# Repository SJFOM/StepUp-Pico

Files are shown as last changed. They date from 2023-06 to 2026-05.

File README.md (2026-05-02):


# *StepUp!* - A no-code tool for instant stepper motor testing

Badge






StepUp device with motor and PCBs

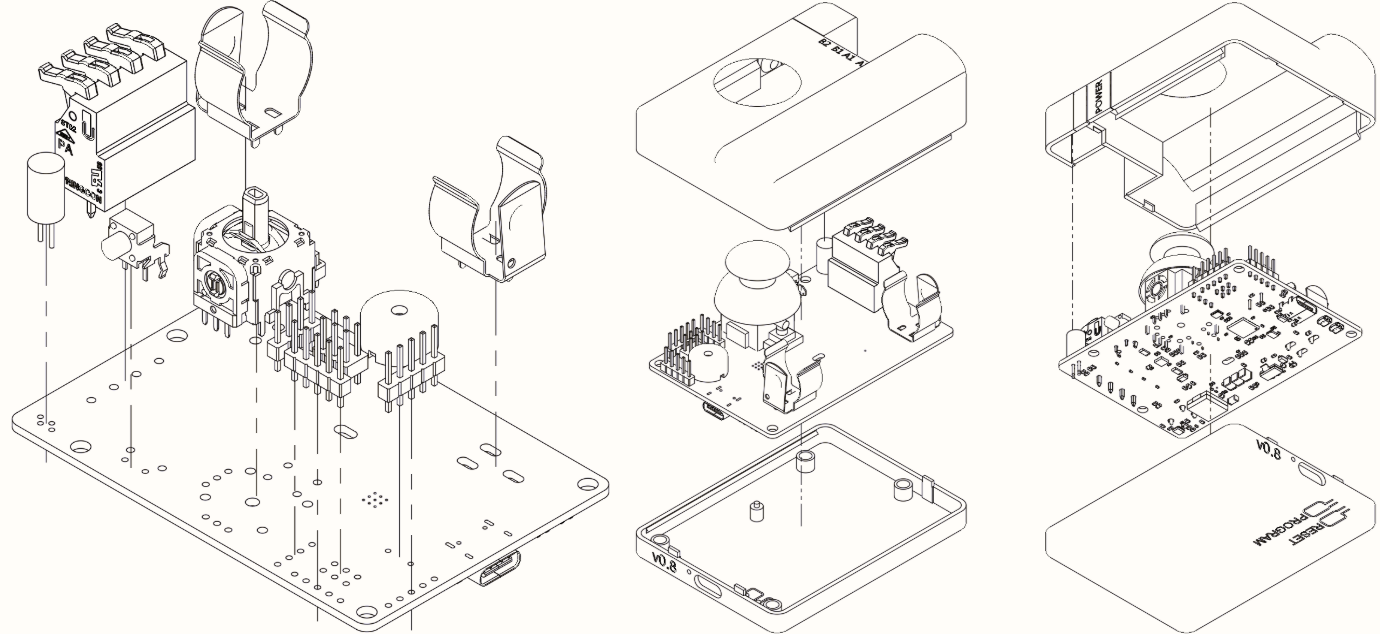
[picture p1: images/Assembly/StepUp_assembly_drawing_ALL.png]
StepUp device with motor


## What is it?
StepUp! is a low-cost, battery powered handheld device for quick testing and development work with any sized stepper motor - all you need is:

- A stepper motor
- A motor cable

## Why did you make it?

Working a lot with stepper motors, I often find myself wanting to test a single motor at a time to understand if its performing as it should - often with questions like:

- Is there an issue with my driving circuit or the motor itself?
- Is the cabling damaged or do the coils contain open or short circuits?
- Does it have a hold current or is it jammed?

I found that, to really answer these questions required power supplies, microcontrollers, stepper motor driving circuitry, a PC to compile and upload firmware and a programmatic approach to moving a motor. What I needed was a simpler way to control motors that felt intuitive - something battery powered and ideally joystick controlled.

I came to the realisation that this problem was two-fold:

1. I don’t have an easy & repeatable way of driving stepper motors
2. I don’t always have all of my lab equipment set up to make the kind of measurements I care about.

>I set out to tackle problem number 1 - creating an easy way to repeatably test a stepper motor

## What makes it special?

There are *plenty* of boards and solutions out there that can drive a stepper motor. However, what I have *yet to see* is a solution that is completely self-contained, requiring no external power supply and driving a stepper motor using input controls from an operator.

My aim is for this to be an item in your toolbox, one that can be called upon whenever you need to test a motor - without all the setup cost.

It is inherently low power - giving just enough juice to get a motor going but with enough power to test out some motor features.

## How much does it cost to build?
### Short answer
Around **€50 (or $60)** per unit

### *Longer answer...*
A core goal from the outset was to make this _as_ cheap as I possibly could. Totting up my most recent order for 5 PCB's with 3 assembled PCBA's and including the additional through-hole components I hand solder to the PCBA's (to reduce cost) works out to around $50 per PCB as per my last order in March 2025.

## Tech specs
- **Firmware:** Pico-SDK `v2.2.0` running FreeRTOS `v11.2.0`
- **CPU:** Dual-core Arm Cortex-M0+ processor, flexible clock running up to 133 MHz
- **RAM:** 264kB on-chip SRAM
- **Flash:** 2MB on-board QSPI flash
- **Battery:** 18650 Li-Ion, single cell (protected or non)
- **Charge current:** 300mA
- **Motor control:** ~10.2V at 500mA (default) -> 5.1 Watts
- **Battery life:** ~5.5 hours in testing using a `3400mAh` 18650 Li-Ion battery

# Pre-requisites

## Assembling a StepUp! device
All documentation and pre-requisites for creating your own StepUp! PCB and enclosure can be found in the [Hardware README file](./Hardware/README.md).

## IDEs

This project was developed using [Microsoft Visual Studio Code](https://code.visualstudio.com/) and all instructions which follow mention use of its code extensions for working with the StepUp! project. Workspace files are included herein - see [rp2040.code-workspace](./rp2040.code-workspace).

## Quick-start - cloning the repo and uploading code

1. Clone (recursively) the repo: `git clone --recursive https://github.com/SJFOM/StepUp-Pico.git`.
2. Enter the repo: `StepUp-Pico`.
3. Optionally, edit `CMakeLists.txt` and `/App-StepUp/CMakeLists.txt` to configure the project.
4. Optionally, manually configure the build process: `cmake -S . -B build/`.
5. Optionally, manually build the app: `cmake --build build`.
6. Connect your device so it’s ready for file transfer.
7. Copy the `StepUp.uf2` file from the `build/App-StepUp` folder to the drive which represents the attached Pico device hardware.

## VS Code extensions

### Required
Raspberry Pi's own [VSCode extension](https://github.com/raspberrypi/pico-vscode) simplifies the installation process for any OS. It includes other necessary VS Code extensions such as [CMake](https://marketplace.visualstudio.com/items?itemName=ms-vscode.cmake-tools) and [Cortex-Debug](https://github.com/marus/cortex-debug) for both CMake file compilation and debugging using OpenOCD via a SWD capable debugger probe respectively.

### Optional
While the Raspberry Pi Pico extension is the only one _required_ to compile code for this project, an ancilliary list of recommended extensions can be found in the included [`extensions.json`](./.vscode/extensions.json) file and will be prompted for install by the VS Code IDE.

## Project Structure

```
/StepUp-Pico
|
|___/App-StepUp             // StepUp! Application source code (C++)
|   |___CMakeLists.txt      // Application-level CMake config file
|
|___/Config
|   |___FreeRTOSConfig.h    // FreeRTOS project config file
|
|___/FreeRTOS-Kernel        // FreeRTOS kernel files, included as a submodule
|
|___/images                 // Image files used in the README.md guides
|
|___/Hardware               // Thin layers for global control - used as parent class
|   |___3D print files      // STL files to be 3D printed for StepUp housing
|   |___PCBA files          // Zip file containing Gerbers, Drill files & BoM 
|
|___/Interfaces             // Thin layers for global control - used as parent class
|
|___/Libraries              // Non-HW specific code, commonly used function calls
|
|___CMakeLists.txt          // Top-level project CMake config file
|___pico_sdk_import.cmake   // Raspberry Pi Pico SDK CMake import script
|
|___rp2040.code-workspace   // Visual Studio Code workspace
|
|___README.md
|___LICENSE.md
```

# Using the device

Steps `1` -> `3` below should be followed in the order provided to give best chances of uploading code first time!

If helpful, all PCB schematics for this project can be found in the [Releases section of my KiCad repository](https://github.com/SJFOM/KiCad/releases).

## 1. Inserting a battery
Only 18650 Li-Ion cells are supported by this device. The 18650 cell can either include battery protection circuitry or not - there is a battery protection circuit on-board the StepUp! device which is configured specifically for the device and will prevent device power-on if reverse polarity is detected. See the [Hardware README file](./Hardware/README.md) for reference on assembly process.

>**NOTE:** When first inserting the battery, you must also plug in a USB C cable to power up the device. This is a known quirk of the battery protection circuit which prohibits using the battery until external power is first applied.

## 2. Uploading code to the device

Once a battery has been inserted, plug the device into your PC using a USB C data cable. 

Due to a small hardware quirk, you need to ensure that the `POWER` button (on the side) is held down for the duration of the programming process. Follow these steps to upload code:
1. Press and hold the `POWER` button on the side of the PCB (or Enclosure box) and the `PROGRAM` button on the bottom of the PCB (or Enclosure box)
3. Press once the `RESET` button to reboot the device into program mode.
4. You can now release the `PROGRAM` button but keep the `POWER` button held down

The device should evaluate as a USB drive mounted to your PC. From here, you can copy the `StepUp.uf2` file to the mounted device either:
- By grabbing the latest copy of [Release firmware](https://github.com/SJFOM/StepUp-Pico/releases) available in the GitHub repo
- _OR_ - locating it in the `build/App-StepUp` directory once you have compiled this repository

Only _now_, once the device has been successfully programmed can you release the `POWER` button.

## 3. Powering ON
Once firmware has been loaded successfully - press and hold the `POWER` button on the side of the device until the LED flashes GREEN several times and an audible tone of increasing frequencies plays (like a step-up sequence).

## 4. Controlling the Motor
### Connection
Connect the stepper motor using the connector labelled with `A1, A2, B1, B2` to match the coils of the given motor, lifting the 4 black tabs of the connector to allow insertion of the wires and then closing each of the 4 black tabs down with an audible "click" once the wires are in place. The wires should ideally have at least 5mm of exposed wire to ensure a good connection.

### Joystick control
The Joystick is used to control the motor direction and speed. If you increase or decrease the speed of the motor and then return the joystick to the center, the next time you move the motor the device will attempt to ramp up to the previous speed the motor was running at. To reset this behaviour to the original starting speed, press the joystick button.

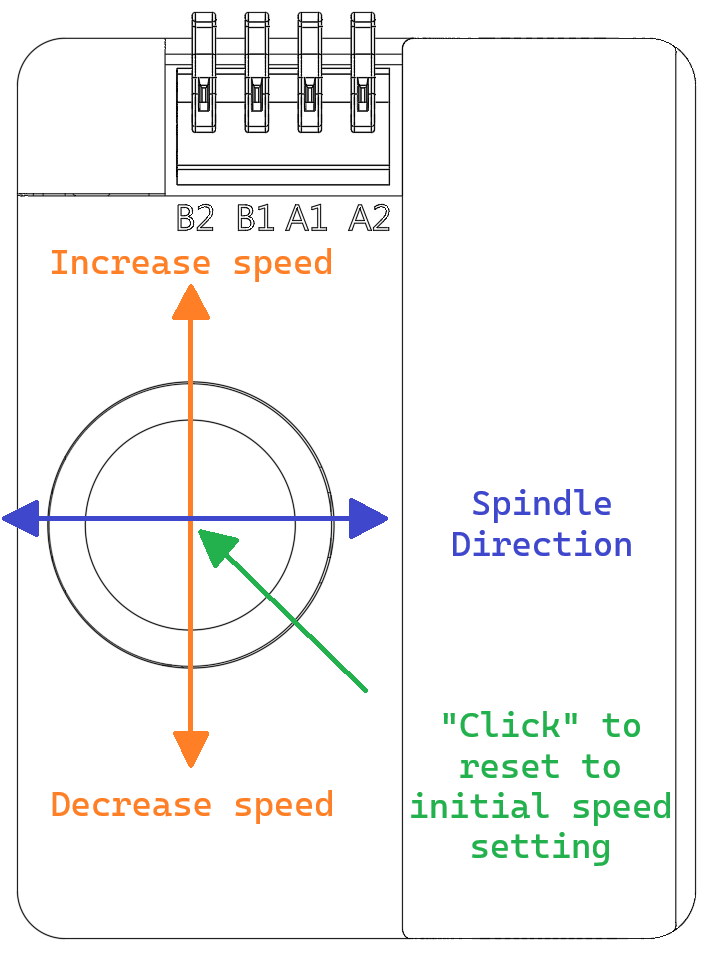
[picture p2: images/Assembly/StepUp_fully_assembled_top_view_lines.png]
Motor joystick control diagram


### Motor current
By default, the StepUp! device drives the supplied stepper motor with `~500mA` of current. While this _can_ be increased by modifying the firmware (see `DEFAULT_IRUN_VALUE` in [`tmc_control.hpp`](./App-StepUp/include/tmc_control.hpp)) it is not recommended given the limited power available from the provided 18650 battery.

## 5. Status Codes

### USB Connection
The StepUp! device emits a stream of serial messages over USB which can be read while the device is operating - especially if any error message needs to be further diagnosed. The following is an example output stream when the device boots - see drop-down item below.

<details open=true>
<summary>StepUp! USB boot-up serial logs</summary>

```
[INFO] App: StepUp 1.0.0 (9134303:2)
[INFO] Setting up peripherals...
[INFO] Watchdog setup...
[INFO] Watchdog setup... OK
[INFO] Buzzer setup...
[INFO] Buzzer setup... OK
[INFO] LED setup...
[INFO] LED setup... OK
[INFO] TMC2300 setup...
[INFO] TMC - UART pins enable
[INFO] TMC2300 silicon version: 0x40
[INFO] Configure TMC2300 default values...
[INFO] TMC2300 GSTAT register diagnostics:
[INFO]  - Reset?: 1
[INFO]  - Driver shutdown due to error?: 0
[INFO]  - Low supply voltage?: 0
[DATA] Run current: 515 mA
[INFO] Configure TMC2300 default values - OK!
[INFO] TMC2300 setup... OK
[INFO] Boost converter setup...
[INFO] Boost converter setup... OK
[INFO] Voltage monitoring setup...
[DATA] Battery voltage: 4.15V
[INFO] Battery voltage monitoring setup... OK
[DATA] Motor voltage: 10.25V
[INFO] Boost/Motor voltage monitoring setup... OK
[INFO] Voltage monitoring setup...OK
[INFO] Joystick setup...
[DATA] X - Raw value: 2048 - voltage: 1.65V
[DATA] Y - Raw value: 2048 - voltage: 1.65V
[INFO] Joystick setup... OK
[INFO] Setting up peripherals... OK!
[INFO] FreeRTOS timer started successfully!
[INFO] TMC is ready for use
```
</details>

### `STANDBY` - When not controlling a stepper motor
| Status | Color: Pattern | Buzzer Pattern | Meaning |
|---|:---:|:---:|---|
| Power ON | Green: Fade, low to high | Sequence, low to high | Device is booting - boot complete once tone completes |
| Power ON | Green: Fade, low to high -> Slow blinking Red for 5 seconds -> Solid Red LED | Sweep, low to high -> Continuous beep tone for 5 seconds | Device is booting - fails during boot |
| Ready | Green: Solid | None | Device is ready, LED colour indicates battery HIGH |
| Ready | Orange: Solid | None | Device is ready, LED colour indicates battery MEDIUM |
| Ready | Red: Solid | None | Device is ready, LED colour indicates battery LOW |
| Power OFF | Red: Fast Blinking | Long continuous | Battery critically LOW - Device auto-powers OFF|
| Power OFF | Red: Fast Blinking | Sequence, high to low | User has triggered a power OFF sequence |

### `ACTIVE` - When controlling a stepper motor
| Status | Color: Pattern | Buzzer Pattern | Meaning |
|---|:---:|:---:|---|
| Joystick button press | Blue: Fast blinking | Two quick beeps | Reset motor speed to initial starting value |
| Motor moving | Red: Rapid Blinking | Three long beeps | Error detected - issue could be any of the following: Short circuit in motor coils, Open circuit, TMC Overheating, battery voltage out of bounds, motor voltage out of bounds |
| Motor moving | White: Solid for ~1 second | None | Momentary motor stall event, unable to provide full power due to excessive motor speed. **Note:** A stall event may occur and the motor will happily continue spinning, it is purely indicative of the loading on the motor driver circuitry |

## 6. Powering OFF
Press and hold the `POWER` button on the side of the device for 5 seconds until the LED flashes RED several times and an audible tone of decreasing frequencies plays (like a step-down sequence).

>**NOTE:** The device has an auto power-down feature and will automatically power OFF after 10 minutes of inactivity.

## Charging

When the USB cable is inserted, a small orange LED near the USB port will illuminate indicating the battery is being charged. The battery is fully charged once the LED extinguishes.

>**NOTE:** The StepUp! PCB charges at a modest 300mA. While not the fastest charging speed out there, it is safe and keeps the temperature of the onboard charging IC down.

# Debugging

>**NOTE:** The device must first be powered **ON** for debugging to be enabled.

While any debug probe offering SWD debugging will work, this project makes use of the very handy [Raspberry Pi Debug Probe](https://www.raspberrypi.com/documentation/microcontrollers/debug-probe.html) and the [`launch.json`](./.vscode/launch.json) file in this repository is configured as such for use with this probe.

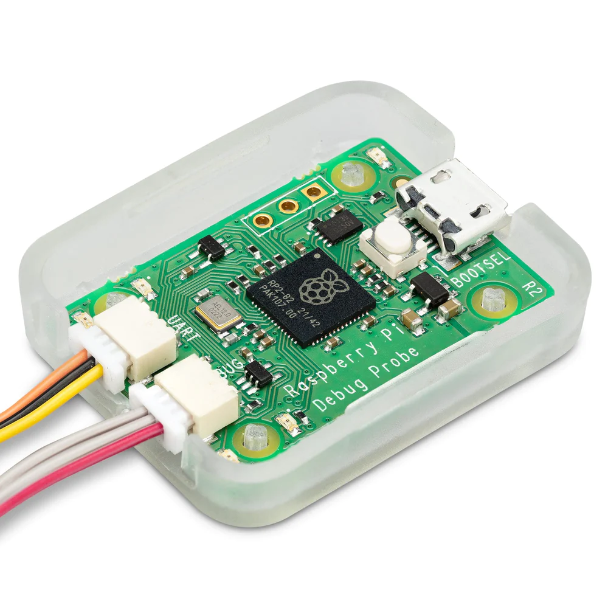
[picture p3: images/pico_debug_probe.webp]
Pico Debug Probe


A debugging session can be started either through the Raspberry Pi Pico extension or by using the `Run and Debug` extension in the VS Code sidebar. In either case, use the `Pico Debug (Cortex-Debug)` prompt when asked how you want to initalise the session.

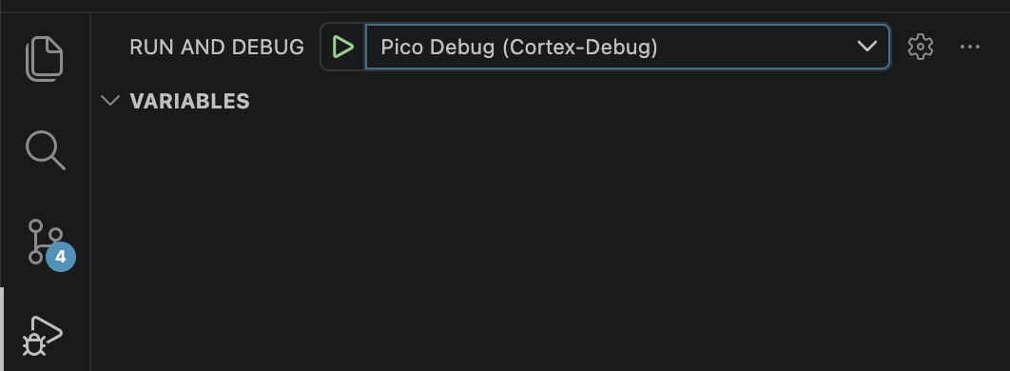
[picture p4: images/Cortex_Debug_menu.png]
Debug menu


## Debugging on MacOS
To get openocd to play ball, you must install the following libraries as described in the [`openocd/README.macOS` file](https://openocd.org/doc-release/README.macOS):
```bash
brew install libtool automake libusb libusb-compat hidapi libftdi
```

## Debugging in Linux

### Enable `arm-none-eabi-gdb`
To debug in Linux, you need to ensure you have `arm-none-eabi-gdb` installed. If you can build firmware for the Pico, odds are this is already installed on your PC but not symlinked correctly. To link this, run the following with elevated priveleges (`sudo`)
```shell
ln -s /usr/bin/gdb-multiarch /usr/bin/arm-none-eabi-gdb
```
You should now see that running `arm-none-eabi-gdb` works as expected.

## Note on use Linux for debugging 

To help Linux to recognise the debug probe, you may need to update your `udev` rules 
by following the very useful steps outlined [here](https://forums.raspberrypi.com/viewtopic.php?t=364698). This will configure your udev rules to recognise the Pico plugged in as a CMSIS-DAP interface.

The relevant steps in the linked guide are as follows:
1. Create a file `10-my-usb.rules` in `/etc/udev/rules.d` containing
    ```shell
    SUBSYSTEM=="usb", ATTRS{idVendor}=="2e8a", ATTRS{idProduct}=="000c", MODE="666", GROUP="plugdev"
    ```
2. Now, restart the udev service using
    ```shell
    sudo udevadm control --reload
    sudo udevadm trigger
    ```

## Credits

This work makes heavy usage of Tony Smith's (a.k.a [smittytone](https://github.com/smittytone)) wonderful [RP2040-FreeRTOS Template](https://github.com/smittytone/RP2040-FreeRTOS) which forms the basic structure for most of this project. Kudos to his work on creating a simple platform to get started with FreeRTOS on the Pi Pico hardware.

## Copyright and Licences

StepUp! application source © 2026, Sam O'Mahony (a.k.a [SJFOM](https://github.com/SJFOM)) and licensed under the terms of the [MIT Licence](./LICENSE.md).

Original template source code © 2022, Tony Smith (a.k.a. [smittytone](https://github.com/smittytone)) and licensed under the terms of the [MIT Licence](./LICENSE.md).

[FreeRTOS](https://freertos.org/) © 2021, Amazon Web Services, Inc. It is also licensed under the terms of the [MIT Licence](./LICENSE.md).

The [Raspberry Pi Pico SDK](https://github.com/raspberrypi/pico-sdk) is © 2020, Raspberry Pi (Trading) Ltd. It is licensed under the terms of the [BSD 3-Clause "New" or "Revised" Licence](https://github.com/raspberrypi/pico-sdk/blob/master/LICENSE.TXT).

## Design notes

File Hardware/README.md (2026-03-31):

# StepUp! Assembly guide

# Folder Structure
```
/Hardware/3D print files
|
|___/3D print files                                   // Files for 3D printing the StepUp! project enclosure
|
|___/PCBA files/v1.0                                  // Files for re-creating the StepUp! PCBA
|   |___Hand Assembly
|       |___BoM - Hand Assembly components.csv        // Bill of Materials for through-hole hand-assembly components
|       |___Interactive BoM.html                      // Interactive HTML file to assist with component assembly process
|   |___/Manufacturing files
|       |___BoM                                       // Bill of Materials for PCBA
|       |___Gerbers & Drill files.zip                 // Manufacturing files for PCBA production
|       |___Pick & Place.zip                          // Manufacturing files for PCBA production
|   |___STEP                                          // 3D file of PCB
|
|___README.md
```

# Pre-requisites
To fully assembly 1 x StepUp! device - you will need the following
- 1 x StepUp! PCBA - assembled with Top-side SMD components
- 1 x Hand Assembly bottom side components - see "BoM - Hand Assembly components.csv"
- 1 x 3D printer
  - ~50g of PLA or PETG filament for the Top and Bottom sections of the enclosure
  - ~5g of translucent PLA or PETG filament
- 1 x soldering iron & spool of solder
- 1 x 18650 Li-Ion battery (recommended: 2500mAh or higher)
- 1 x Joystick rubber head piece (see [link](https://www.ifixit.com/en-eu/products/playstation-dualsense-controller-joystick-cover) or similar)
- 4 x M3x5.7 threaded inserts
- 4 x M3x5 bolts (hex-head preferable)

# PCBA Assembly
The PCBA comes with one side populated with SMD components but still requires some assembly by hand - this is in an effort to reduce overall build costs by doing some of the through-hole assembly in person. This is also a design choice to enable all the UI elements to exist on one side of the PCB (joystick, LED, motor connector etc..).

## Part 1 - PCB creation and SMD component placement

Using your own preference of PCB manufacturer, upload the manufacturing files located in the `Manufacturing files` folder within this directory. This design uses a 4-layer PCB - if prompted for the layer stackup, the following reference can be used:

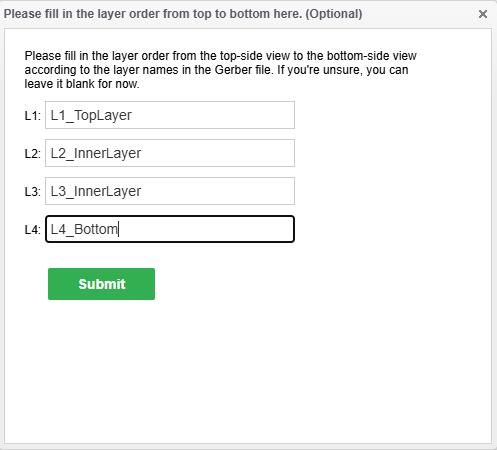
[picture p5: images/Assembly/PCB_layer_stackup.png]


## Part 2 - Hand Assembly of Bottom side components

The bottom side of the PCB is solely populated by through-hole components which are to be assembled by hand. The `BoM - Hand Assembly components.csv` file can be found in the `Hand Assembly` folder and the components there-in should be purchased prior to assembly (as per the pre-requisites section above).

Once you have the components and PCBA to hand, you may reference the `Interactive BoM.html` file as a handy guide for placing the components on the PCB. Additionally, the diagram below shows a 3D perspective of where the through-hole components are located on the PCB.

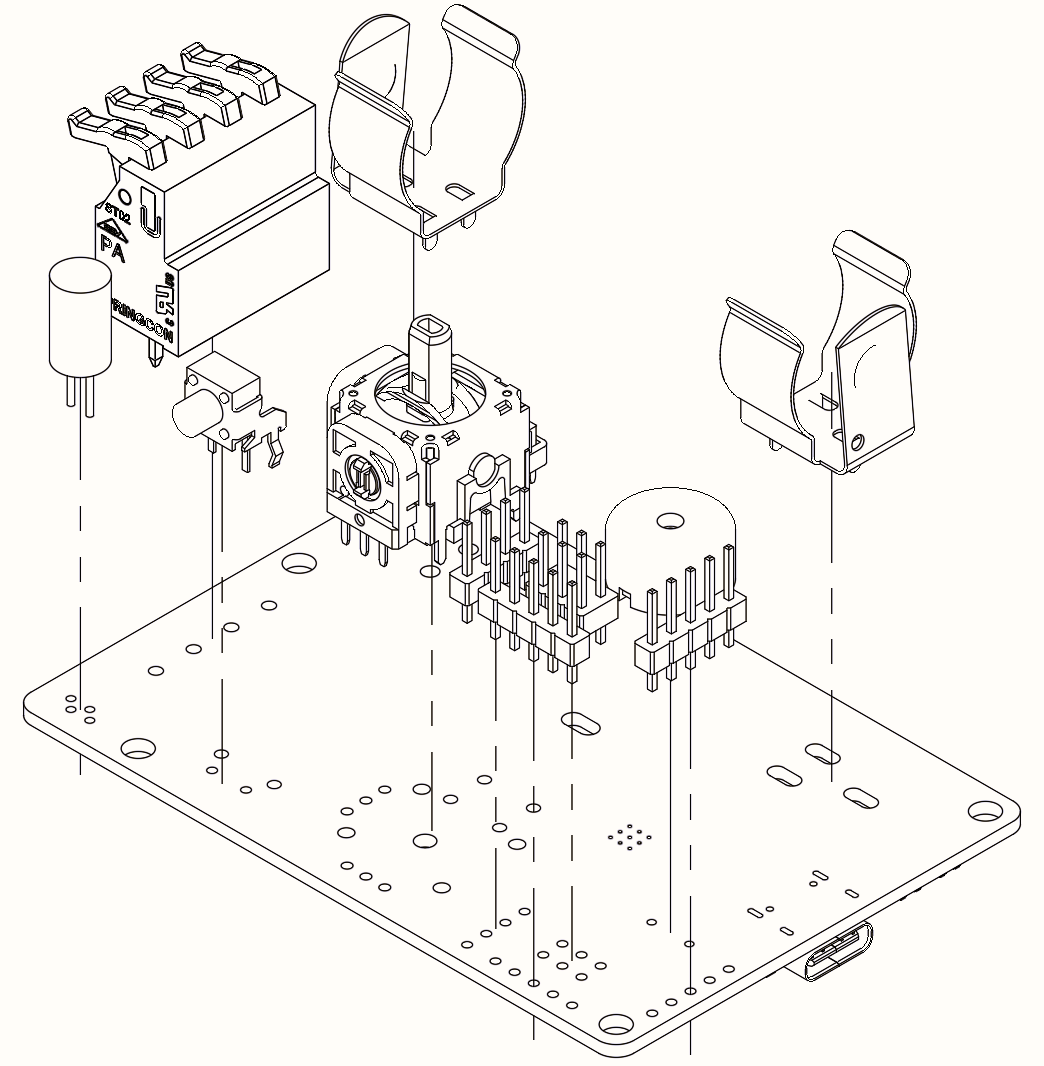
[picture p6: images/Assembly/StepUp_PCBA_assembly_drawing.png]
PCBA Drawing


### Note on Battery clip positioning
When soldering in the negative polarity battery clip, you have the choice of positioning the clip to suit your own 18650 battery as these do not always come in at `65mm` in length. Often, a battery has built-in protection circuitry included will measure around `67mm` (or longer) and so the user may adjust the position of this negative terminal battery clip and solder it in place for their own use case.

# LED Box assembly
With the aid of a small drop of cyanoacrylate (a.k.a super-glue), slide the translucent LED Box onto the Top section of the enclosure housing so that the LED Box is flush to the part.

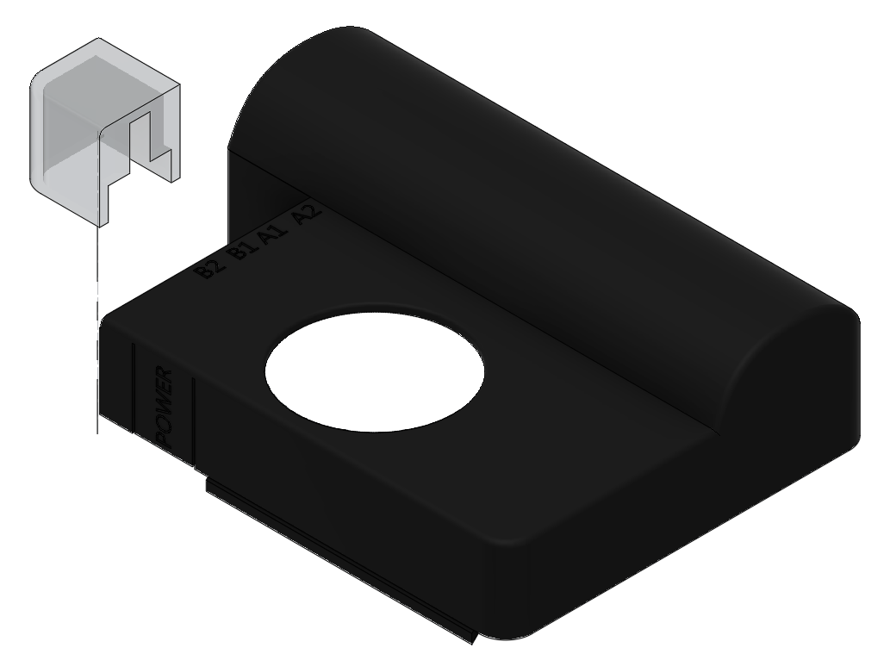
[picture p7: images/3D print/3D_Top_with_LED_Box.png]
LED Box assembly

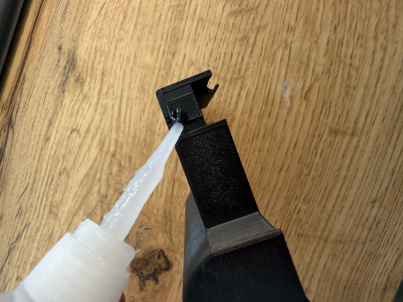
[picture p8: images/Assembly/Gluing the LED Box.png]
LED Box gluing


# Threaded inserts

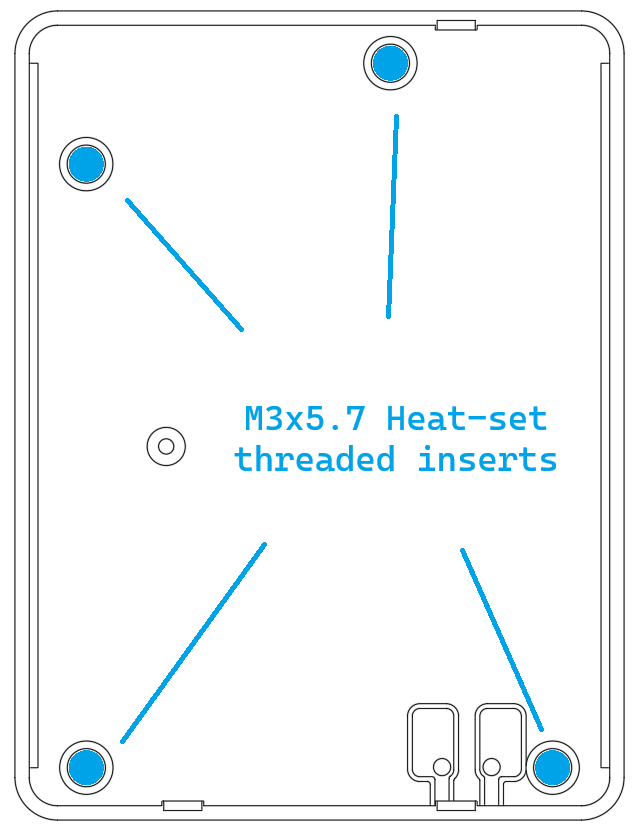
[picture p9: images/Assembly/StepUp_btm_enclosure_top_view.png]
Threaded insert locations

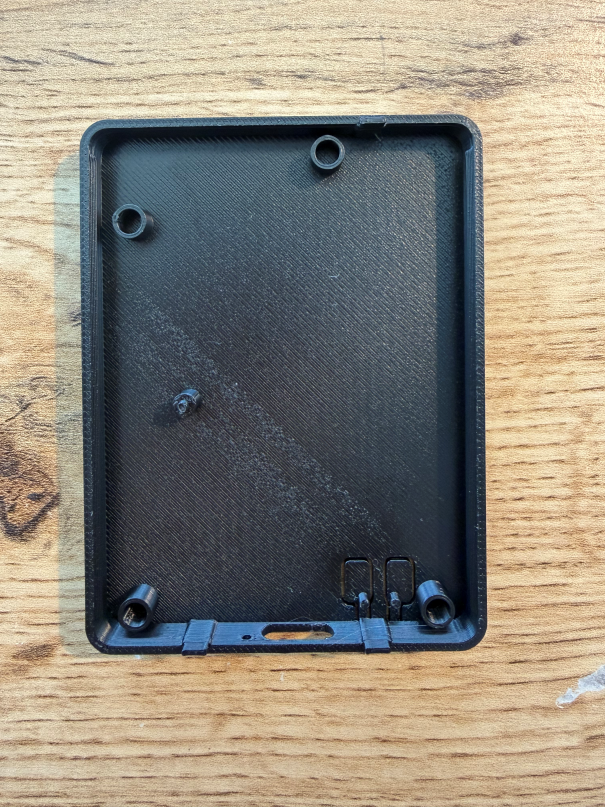
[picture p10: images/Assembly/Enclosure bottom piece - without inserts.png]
Threaded inserts - before assembly

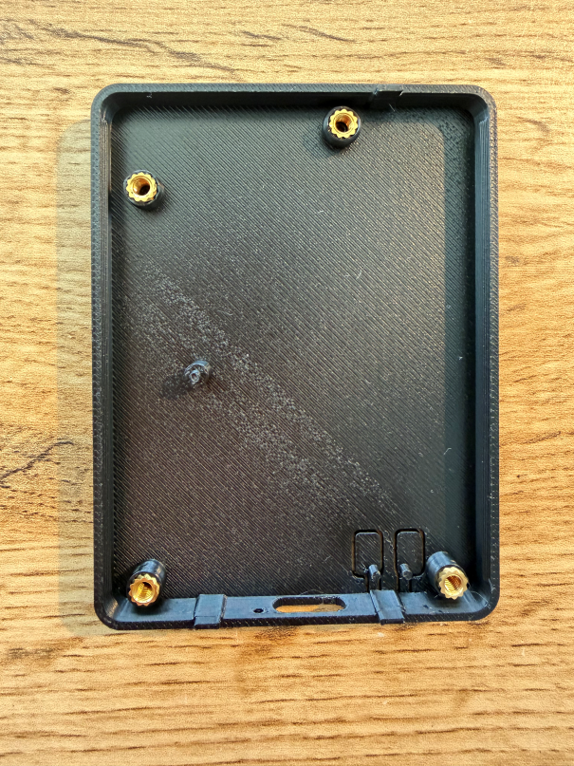
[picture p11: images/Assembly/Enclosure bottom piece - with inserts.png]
Threaded inserts - assembled


## Important - ensure the inserts are set flush
Threaded inserts - incorrect
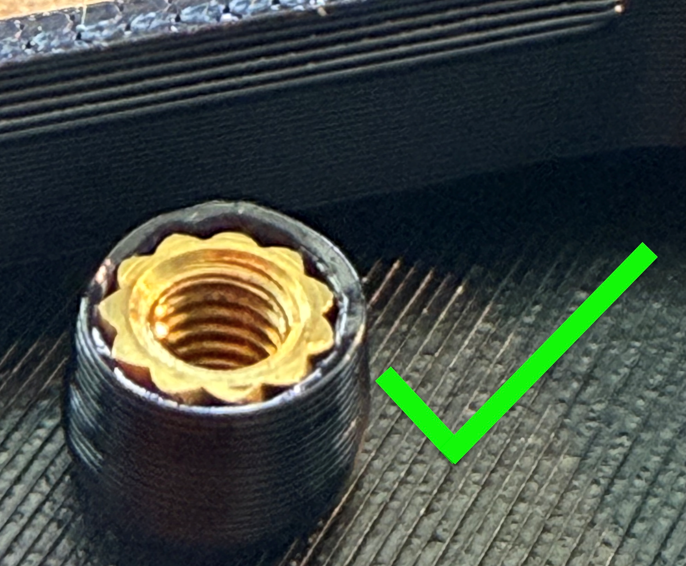
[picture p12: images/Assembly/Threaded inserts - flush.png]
Threaded inserts - correct


# Attaching PCB to Bottom enclosure
Using 4 x M3x5 screws, attach the PCB to the bottom housing assembly as shown in the image below - do not overtighten these screws as they may damage the PCB.

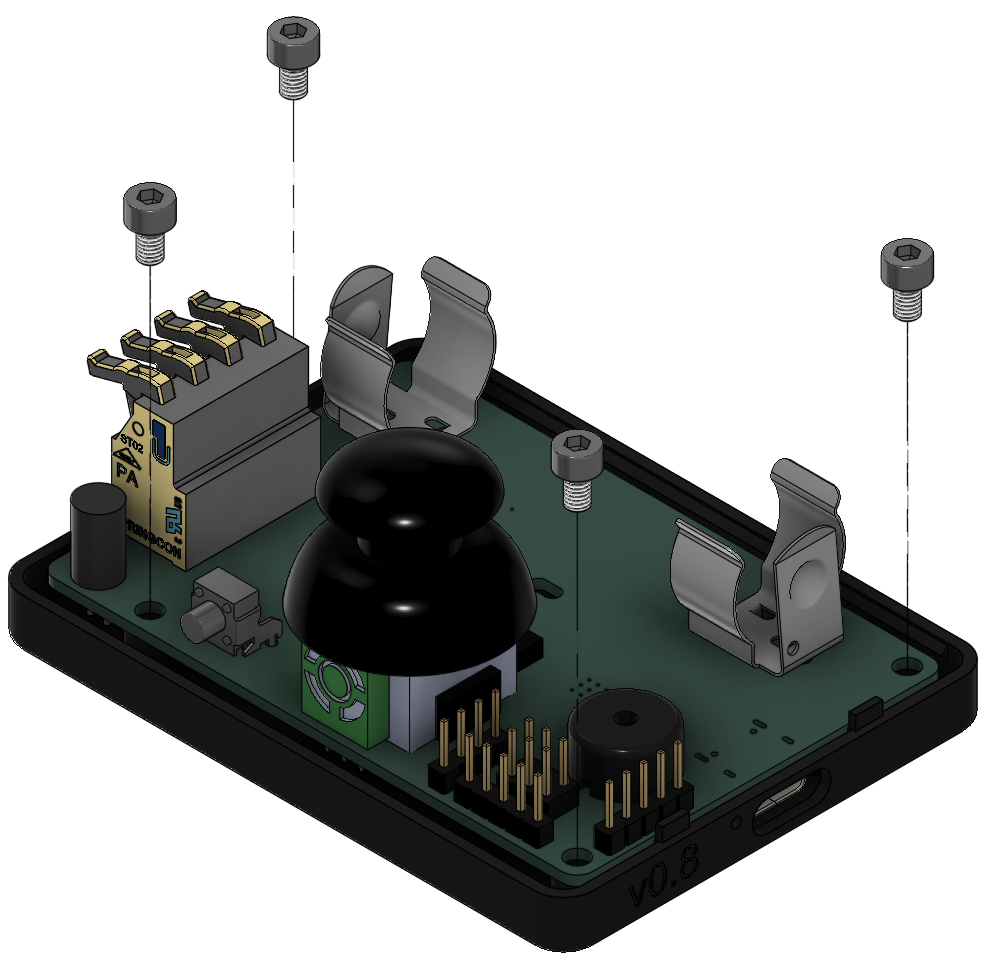
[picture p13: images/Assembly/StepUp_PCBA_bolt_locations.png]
Enclosure bolt locations


# 3D printed housing assembly

Once the PCBA is attached to the bottom assembly, the top piece should just click into place.

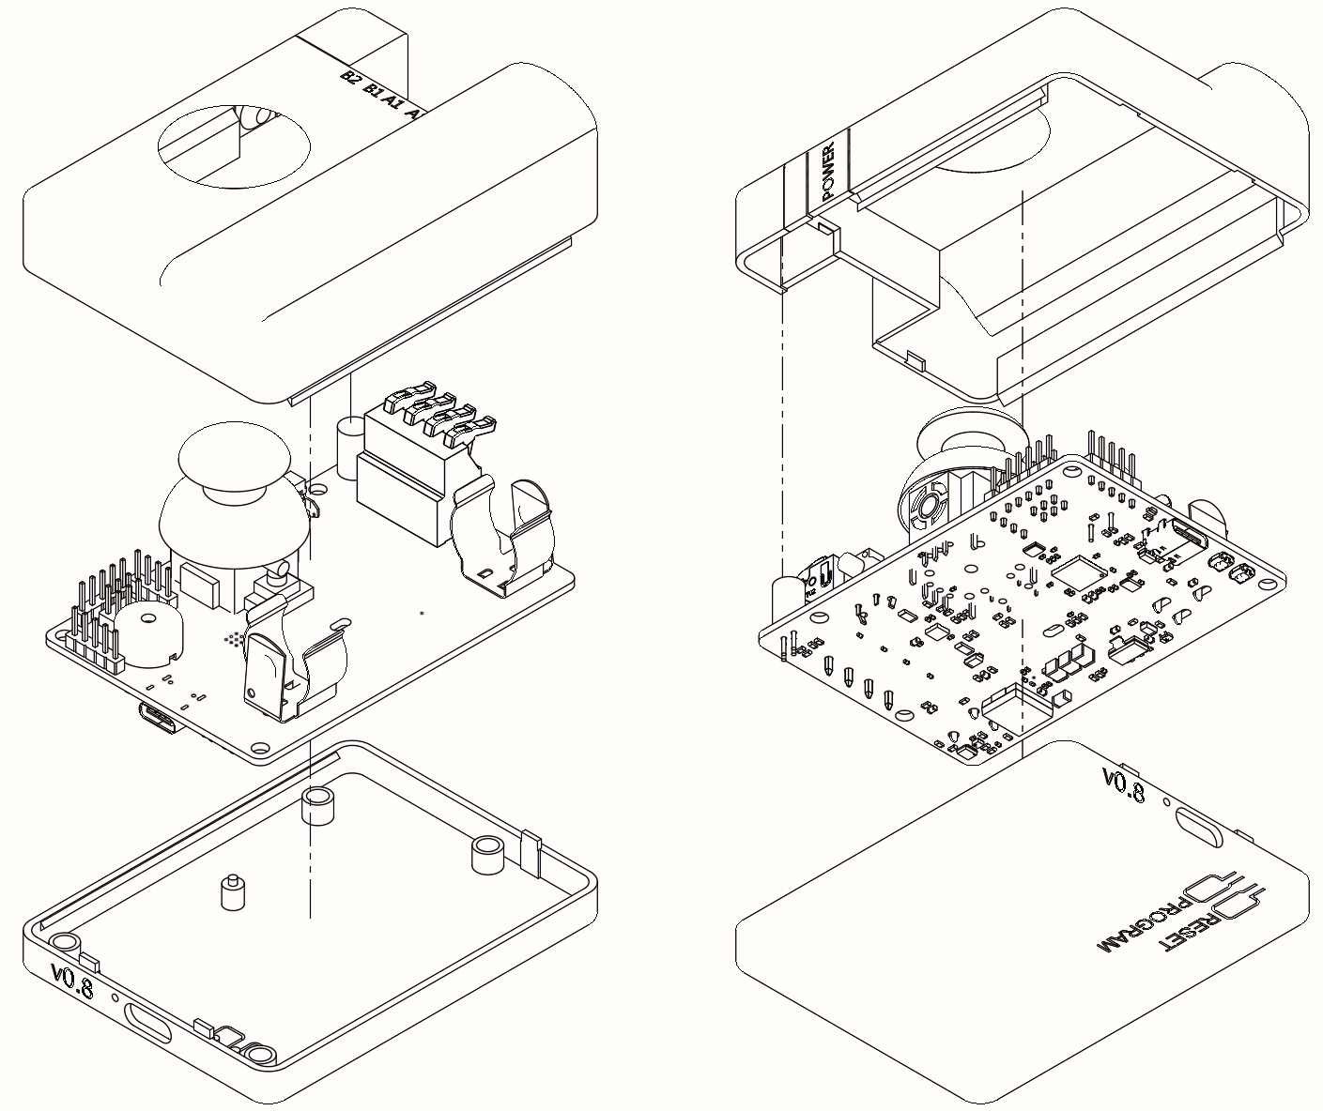
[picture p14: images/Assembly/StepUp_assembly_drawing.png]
StepUp exploded assembly view


# [Optional] Zip-tie support for retaining battery

There is a small likelihood that the battery may become momentarily dislodged during device use if it falls on a hard surface or is shaken vigorously. With this in mind, there is an opening in the PCB which the user may route a zip-tie through to secure the battery in place

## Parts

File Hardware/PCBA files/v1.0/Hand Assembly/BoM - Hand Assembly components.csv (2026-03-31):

 | Sourced | Placed | References | Value | Footprint | Quantity
1 |  |  | SW3 | 1825027-8 | 1825027-8 | 1
2 |  |  | BT1 | 54 | 54 | 1
3 |  |  | BT2 | 54 | 54_SLOT | 1
4 |  |  | BZ1 | PS1240P02CT3 | PS1240P02BT | 1
5 |  |  | JOY1 | THB001P | THB001P | 1
6 |  |  | LED2 | MP008267 | MP008267 | 1
7 |  |  | LOGO1 | Zip-tie | LOGO | 1
8 |  |  | J2 | Conn_01x05_Pin | PinHeader_1x05_P2.54mm_Vertical | 1
9 |  |  | J3 | Conn_01x04_Pin | PinHeader_1x04_P2.54mm_Vertical | 1
10 |  |  | J4 | Conn_02x03_Odd_Even | PinHeader_2x03_P2.54mm_Vertical | 1
11 |  |  | J5 | AST0250404 | AST250404 | 1
12 |  |  | J6 | Conn_01x05 | PinHeader_1x05_P2.54mm_Vertical | 1

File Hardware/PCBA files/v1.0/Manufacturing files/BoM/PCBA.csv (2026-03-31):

Reference | Value | Qty | Package | Manufacturer | MPN
C1,C2 | 15pF | 2 | 0402 | YAGEO | CC0402FRNPO9BN150
C3,C4,C5,C7,C9,C10,C11,C12,C13,C14,C15,C17,C18,C19,C26,C29,C39,C40,C41,C42,C43,C44 | 0.1uF | 22 | 0402 | Murata | GRM155R61C104KA88D
C6,C8,C24,C32,C37 | 1uF | 5 | 0603 | Murata | GRM188R71E105KA12D
C16,C28,C38 | 10uF | 3 | 0603 | Murata Electronics | GRM188R61E106KA73D
C20,C21,C22,C23 | 470pF | 4 | 0402 | YAGEO | CC0402KRX7R0BB471
C25 | 22uF | 1 | 1206 | Murata | GRM319R61C226KE15D
C27,C30,C31 | 4.7uF | 3 | 0603 | AVX | 0603ZD475KAT2A
C33 | 4700pF | 1 | 0402 | Murata | GRM155R61H472KA01D
C34,C35,C36 | 22uF | 3 | 1210 | Murata | GRM32ER71E226KE15L
D1,D12 | 1N4148W-TP | 2 |  | Micro Commercial Co | 1N4148W-TP
D2 | SMF12A | 1 |  | Vishay | SMF12A-M3-08
D3,D4,D5,D6,D7,D8,D9,D10 | B5819W-TP | 8 |  | Micro Commercial Co | B5819W-TP
D11 | BAT54C-7-F | 1 |  | Diodes Incorporated | BAT54C-7-F
J1 | USB_C_Receptacle_USB2.0_16P | 1 |  | GCT | USB4105-GF-A
L1,L2,L3,L4 | HI1206T500R-10 | 4 |  | Laird-Signal Integrity Products | HI1206T500R-10
L5 | 1.8uH | 1 |  | Sumida | CDMC8D28NP-1R8MC
LED1 | IN-S63AS5A | 1 |  | Inolux | IN-S63AS5A
Q1 | BSS84 | 1 |  | ON Semiconductor | BSS84
Q2,Q3,Q5,Q6 | 2N7002-7-F | 4 |  | Diodes Incorporated | 2N7002-7-F
Q4 | SSM3J328R_LF | 1 |  | Toshiba Semiconductor and Storage | SSM3J328R,LF
R1,R5 | 1k | 2 | 0402 | YAGEO | RC0402FR-071KL
R3,R4 | 5.1kR | 2 | 0603 | YAGEO | RC0603FR-075K1L
R6,R7 | 27R | 2 | 0402 | YAGEO | RC0402FR-0727RL
R8,R45 | 100R | 2 | 0603 | YAGEO | RC0603FR-07100RL
R9,R10,R11,R12,R13,R14,R15,R16,R33,R40,R41 | 10kR | 11 | 0603 | YAGEO | RC0603FR-0710KL
R17,R51,R53 | 1kR | 3 | 0603 | YAGEO | RC0603FR-071KL
R18,R32,R37,R38,R39,R43,R52 | 100kR | 7 | 0603 | YAGEO | RC0603FR-07100KL
R19,R20 | 150mR | 2 | 1206 | Bourns Inc. | CRL1206-FW-R150ELF
R21,R29,R35 | 0R | 3 | 0603 | YAGEO | RC0603FR-070RL
R22 | 3.3kR | 1 | 0603 | Panasonic | ERJU03F3301V
R23 | 301kR | 1 | 0402 | Vishay-Dale | CRCW0402301KFKED
R24 | 620R | 1 | 0603 | YAGEO | RC0603FR-07620RL
R25 | 17.4kR | 1 | 0402 | Vishay-Dale | CRCW040217K4FKED
R26 | 127kR | 1 | 0402 | Vishay-Dale | CRCW0402127KFKED
R27 | 787kR | 1 | 0402 | Vishay-Dale | CRCW0402787KFKED
R28 | 107kR | 1 | 0402 | Vishay-Dale | CRCW0402107KFKED
R30 | 1Meg | 1 | 0603 | YAGEO | RC0603FR-071ML
R34 | 330R | 1 | 0603 | YAGEO | RC0603FR-07330RL
R36,R46 | 5.1MR | 2 | 0603 | YAGEO | RC0603FR-075M1L
R42 | 56kR | 1 | 0603 | YAGEO | RC0603FR-0756KL
R44 | 2.2kR | 1 | 0402 | YAGEO | RC0402FR-072K2L
R47,R48,R49 | 120R | 3 | 0603 | YAGEO | RC0603FR-07120RL
R50 | 22R | 1 | 0603 | YAGEO | RC0603FR-0722RL
SW1,SW2 | 434153017835 | 2 | None | Würth Elektronik | 434153017835
U1 | W25Q16JVUXIQ TR | 1 |  | Winbond Electronics | W25Q16JVUXIQ TR
U2 | USBLC6-2SC6 | 1 |  | STMicroelectronics | USBLC6-2SC6
U3 | RP2040 | 1 |  | Raspberry Pi | RP2040
U4 | TMC2300-LA-T | 1 |  | ADI Trinamic | TMC2300-LA-T
U5 | LDL1117S33R | 1 |  | STMicroelectronics | LDL1117S33R
U6 | MCP73832T-2ACI_OT | 1 |  | Microchip Technology | MCP73832T-2ACI/OT
U7 | TPS61089 | 1 |  | Ti | TPS61089RNRR
U8 | ECH8697R-TL-W | 1 |  | OnSemi | ECH8697R-TL-W
U9 | BQ29700 | 1 |  | Ti | BQ29700DSER
Y1 | ABM8-272-T3 | 1 |  | Abracon LLC | ABM8-272-T3

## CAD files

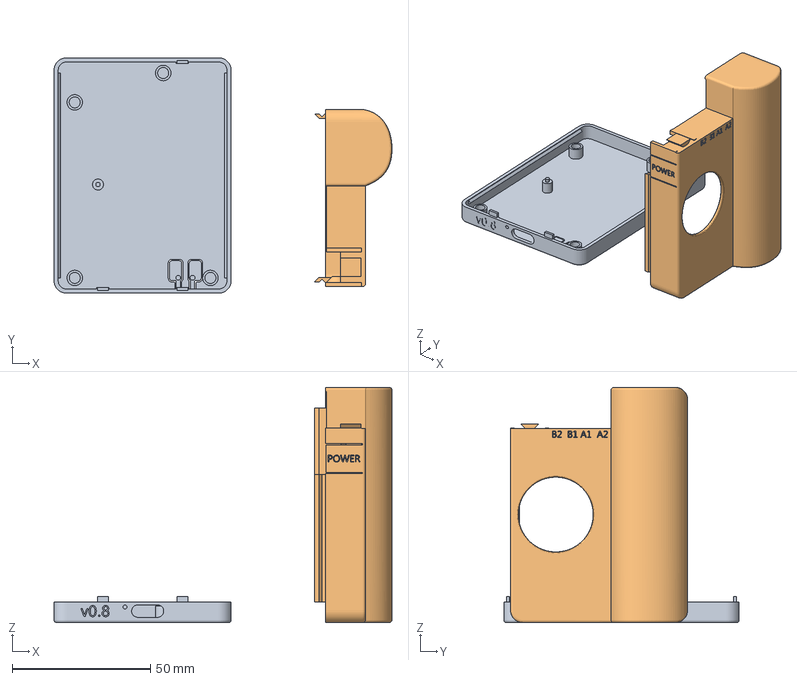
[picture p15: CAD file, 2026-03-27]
Hardware/3D print files/Bambu Labs/Bambu Labs Project - Enclosure.3mf
122.1 x 85.0 x 85.0 mm
Bottom.stl
Top.stl

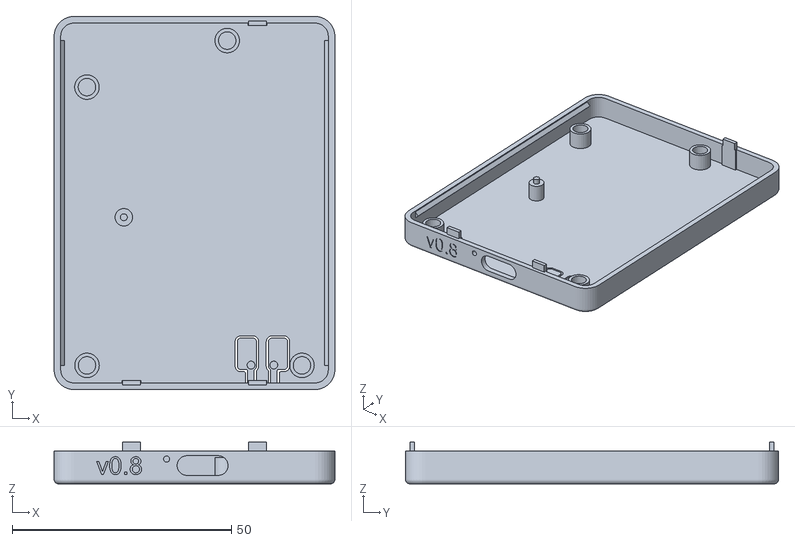
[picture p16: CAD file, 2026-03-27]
Hardware/3D print files/Bottom.stl
64.0 x 85.0 x 9.50

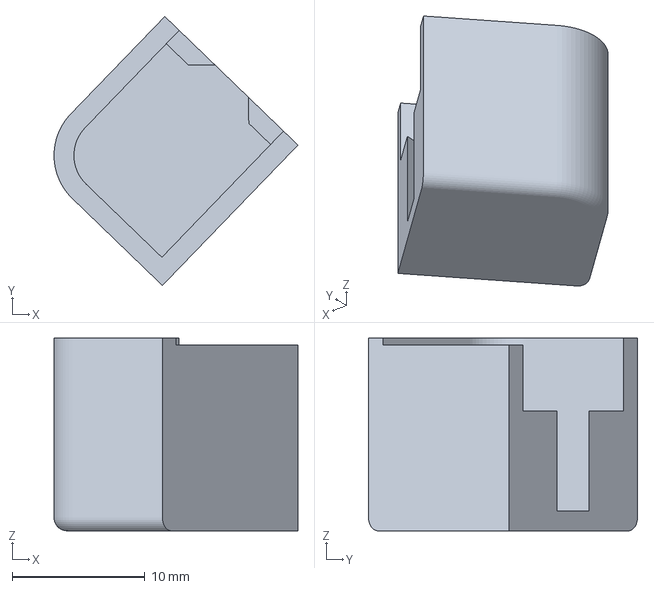
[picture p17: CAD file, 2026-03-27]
Hardware/3D print files/Bambu Labs/Bambu Labs Project - LED Box.3mf
18.4 x 20.2 x 14.5 mm

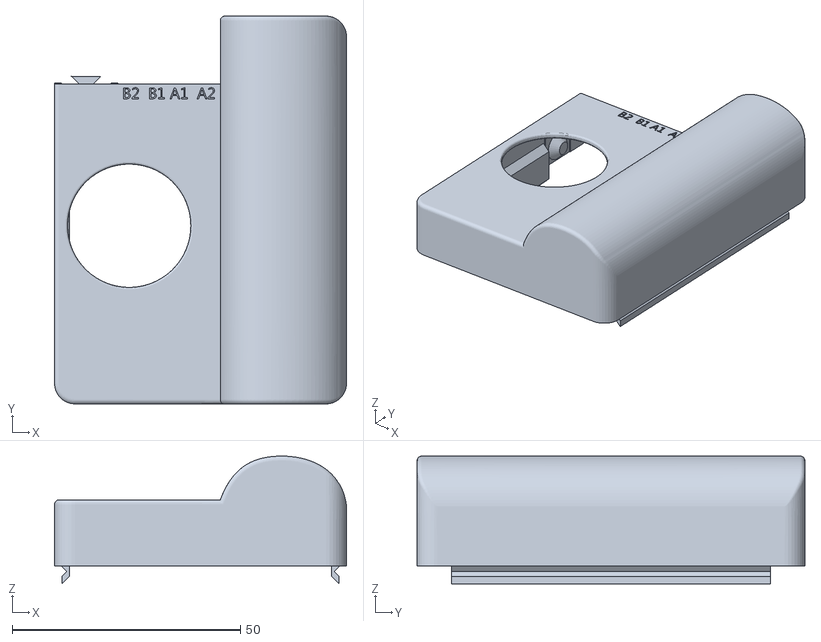
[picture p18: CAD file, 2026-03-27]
Hardware/3D print files/Top.stl
64.0 x 85.0 x 28.0

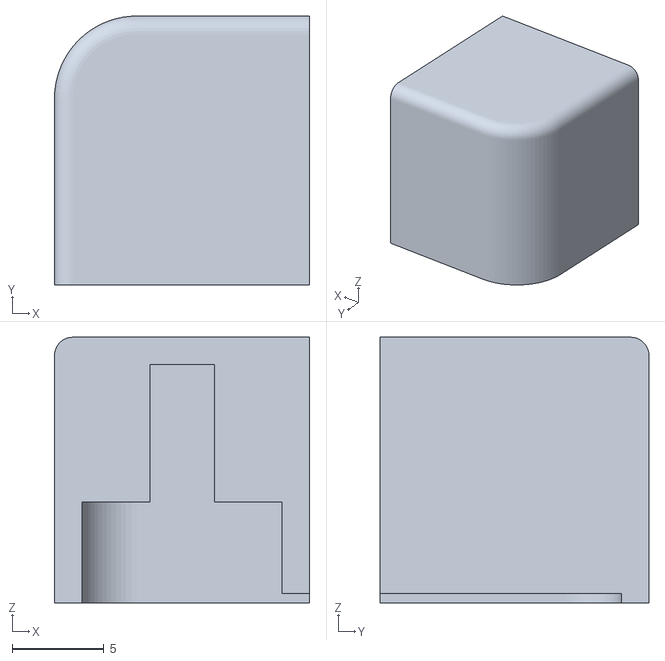
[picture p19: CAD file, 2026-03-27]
Hardware/3D print files/LED BOX.stl
13.9 x 14.7 x 14.5

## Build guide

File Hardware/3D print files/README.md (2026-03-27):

# 3D print files

## Folder Structure
```
/Hardware/3D print files
|
|___/Bambu Labs                                 // Bambu Labs pre-configured project files
|   |___Bambu Labs Project - Enclosure.3mf      // Project file for Top & Bottom 3D print files
|   |___Bambu Labs Project - LED Box.3mf        // Project file for LED Box print file
|
|___Bottom.stl                                  // Enclosure bottom piece 3D print file
|___LED Box.stl                                 // LED Box piece 3D print file
|___Top.stl                                     // Enclosure top piece 3D print file
|
|___README.md
```

## **NOTE:** All measurements below are in millimetres

## Top - print in PLA or PETG

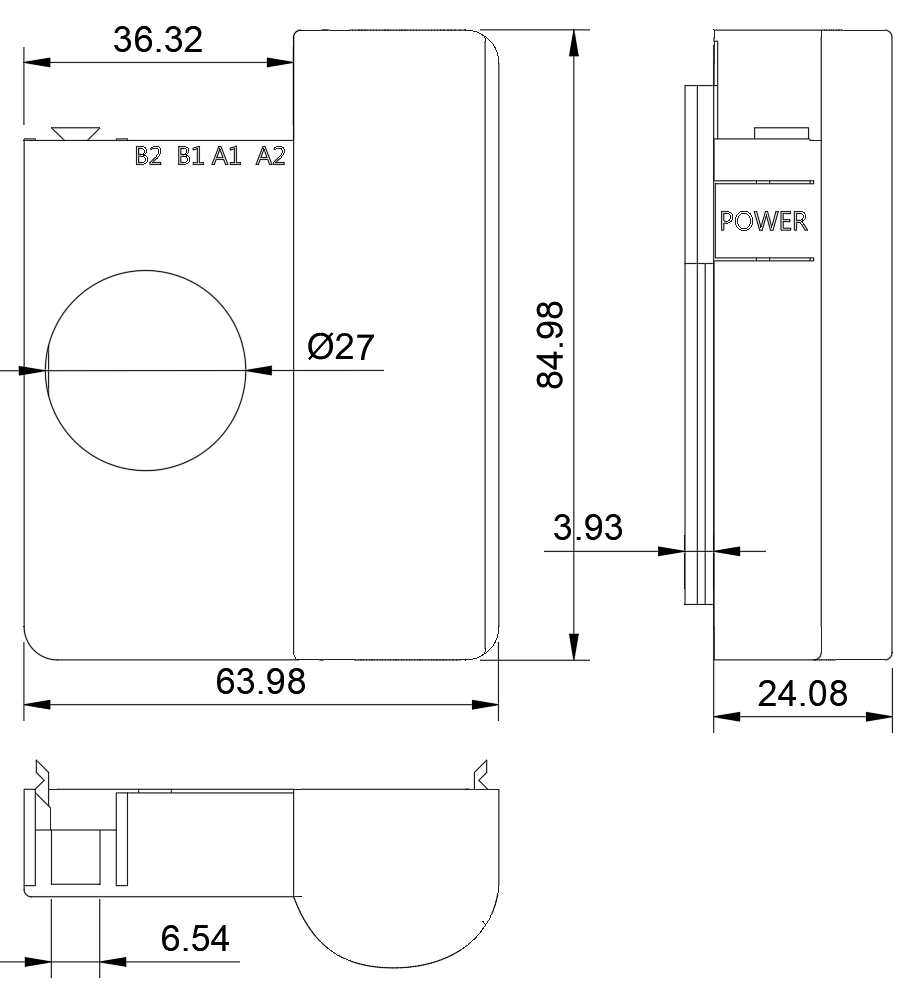
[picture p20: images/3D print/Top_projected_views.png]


## Bottom - print in PLA or PETG
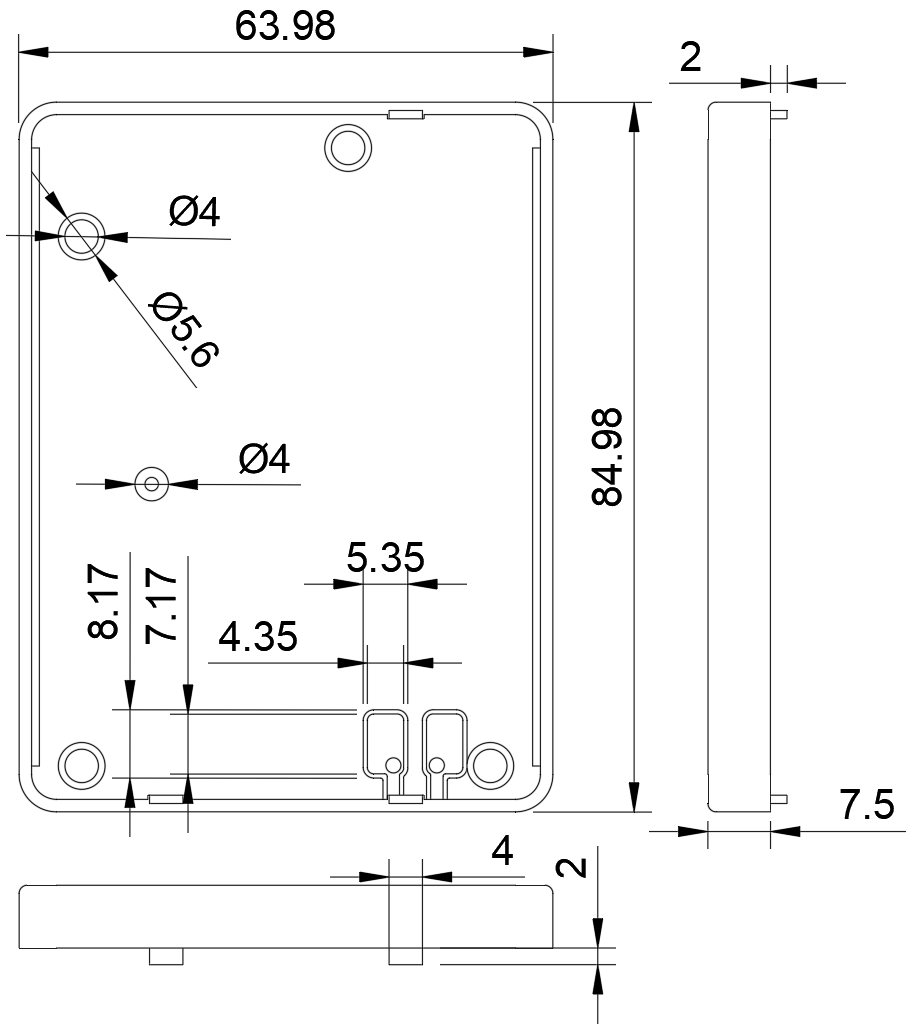
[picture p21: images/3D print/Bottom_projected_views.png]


## LED Box - print in translucent PLA or PETG
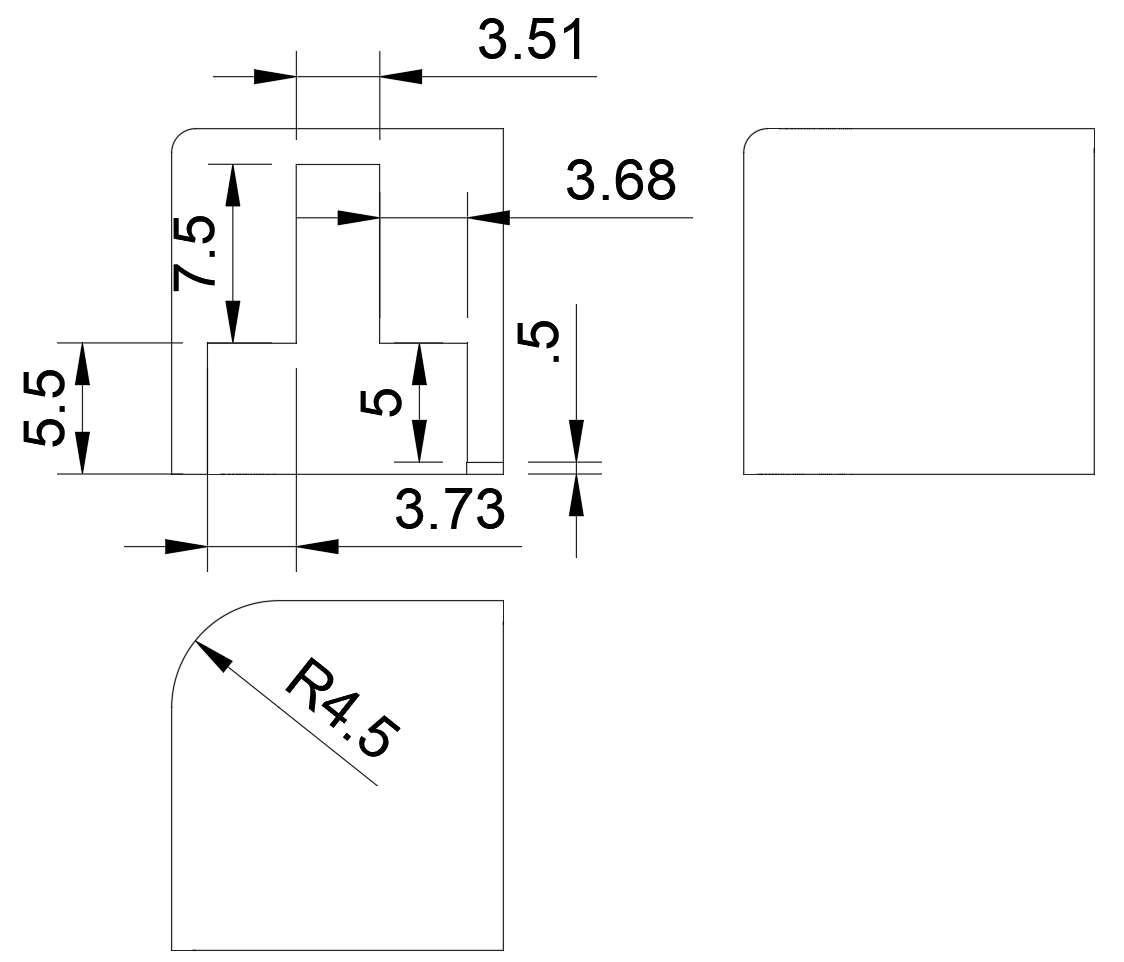
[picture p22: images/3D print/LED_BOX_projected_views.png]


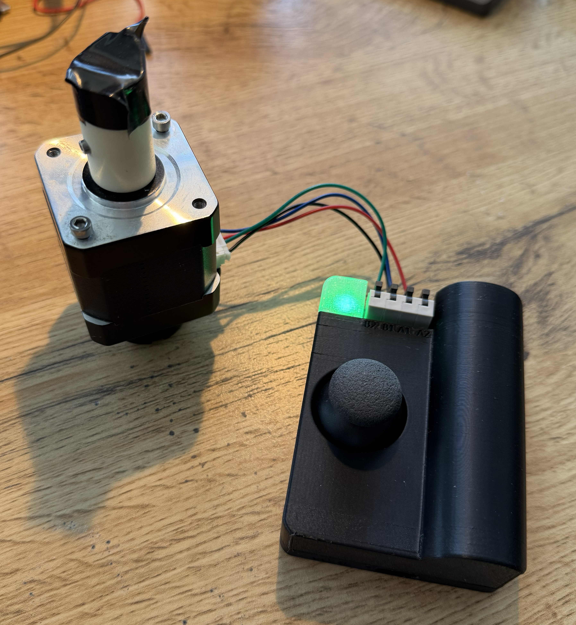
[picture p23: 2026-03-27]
images/Assembly/StepUp_fully_assembled_with_motor.jpg

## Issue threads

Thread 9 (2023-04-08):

Improve parent folder README

SJFOM, 2023-04-08:
Parent folder README is currently unchanged and reflects the previous project template. Let's fix this and make it more project specific.

Closed 2023-06-11.

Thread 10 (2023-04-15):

Analog joystick - initial integration

SJFOM, 2023-04-15:
## Joystick interface
The analog joystick should be integrated with the following criteria met:
- Dedicated `control` class for joystick control
- Class should set up ADC to read X & Y potentiometers
- Class should have a timer which polls ADC state
- Joystick state should be bucketed into various magnitude windows (how far from central position it is)
- main.cpp should have a thread for joystick and retrieve its current state
- The joystick button should be captured as an interrupt and included in the "joystick state" data package returned to main.cpp

Closed 2023-06-11.

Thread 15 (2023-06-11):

Adaptive motor load handling

SJFOM, 2023-06-11:

SJFOM, 2025-04-29:
If the following conditions are met, CoolStep will be enabled to reduce the motor current (`CS_ACTUAL` will reduce)
- `tcoolthresh` must be less than `tstep` - these represent motor velocities
- `sg_result` (seen as `sg_live` here) must be > `sg_upper` (a.k.a `(SEMIN+SEMAX+1)*32`)
- If `sg_result` dips below `sg_upper`, the current `CS_ACTUAL` increases up to `IRUN`

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

Closed 2025-04-29.

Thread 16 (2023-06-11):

Deploy script - OS agnostic

SJFOM, 2023-06-11:

SJFOM, 2025-03-23:
Resolved by moving to using the VS Code Pico plugin in #60

Closed 2025-03-23.

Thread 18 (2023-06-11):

Handle reported TMC error states

SJFOM, 2023-06-11:
The TMC2300 has several potential error states which might cause the driver to cease functioning.

Catching and reporting these as they happen and safely integrating with the function of the motor should be reported to the user in some meaningful way
- Rev1: An error LED

Closed 2024-10-08.

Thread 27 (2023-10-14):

Detect motor open-load or short-circuit states

SJFOM, 2023-10-14:

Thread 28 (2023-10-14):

Implement motion ramp profile over UART

SJFOM, 2023-10-14:
TMC2300 datasheet recommends that you should create a ramp profile for UART driven situations to ensure you don't stall at higher RPM.
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

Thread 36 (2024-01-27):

Enable Stallgaurd threshold functionality

SJFOM, 2024-01-27:

SJFOM, 2024-01-27:
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

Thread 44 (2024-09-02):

USB connection detect

SJFOM, 2024-09-02:
https://www.notion.so/Feature-development-c446f3bc8f3f4633932290f4609e2841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

Use inbuilt special-purpose interrupt for this

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

Closed 2025-03-06.

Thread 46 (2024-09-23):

Enable watchdog timer

SJFOM, 2024-09-23:
https://www.raspberrypi.com/documentation/pico-sdk/hardware.html#hardware_vreg

SJFOM, 2025-04-16:
Implemented in https://github.com/SJFOM/StepUp-Pico/pull/65/commits/8c17b4b10c72c6ec78996b2090b0a8443890b010

Closed 2025-04-16.

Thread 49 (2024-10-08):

Gracefully handle max motor speed

SJFOM, 2024-10-08:
Use careful thresholding against the `PWM_SUM_VALUE` data to infer if the TMC driver is over exerting itself to power the motor.

Report to user when max speed reached (notification)

Closed 2025-06-27.

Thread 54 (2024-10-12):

Open circuit detection does not work at low RPM

SJFOM, 2024-10-12:

Closed 2024-10-12.

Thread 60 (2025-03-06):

Battery voltage monitoring + handling

SJFOM, 2025-03-06:
# Battery monitoring
We want to ensure safe handling of the battery by monitoring the battery voltage and disabling motor control functionality when the voltage is too low

We should also consider monitoring for battery voltage which is too high (although charging circuitry _should_ take care of this eventuality in most cases.

## Approach
Consider a windowed ADC read of the battery voltage to ensure we don't catch the battery voltage under a sudden voltage dip due to surge/in-rush current from a motor.

We will likely want to experimentally monitor the battery voltage when a load is applied (using scope or otherwise) to observe how it fluctuates.

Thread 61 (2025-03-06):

Power down functionality

SJFOM, 2025-03-06:
# Power OFF ⚡
We want the MCU to gracefully handle powering itself OFF when the user asks it to, giving it some discrete sequence of steps which plays the buzzer & lights up LED's to show it is powering down.

## Thoughts
Play a "Step down" tone (opposite of power-on tone) to denote its powering off transition

Closed 2025-04-29.

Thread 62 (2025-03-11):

Tidy up + reduce size of repo

SJFOM, 2025-03-11:
# TO-DO
- Up-rev SDK version to latest and ensure code working
- Current repo size is ~2.5GB - remove Pico SDK and lighten this up

SJFOM, 2025-03-23:
Resolved as part of #60

Closed 2025-03-23.

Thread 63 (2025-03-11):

Acknowledge user power ON

SJFOM, 2025-03-11:
# Power ON confirmation
- Currently, user would intuitively hold power ON button until buzzer emits boot-up sound
- This delay (waiting for TMC2300) could be mitigated in two ways:
1. Optimal: Speed up TMC init sequence
2. Additional beep at start-up

Closed 2025-04-15.

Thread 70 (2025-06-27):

Low battery triggers constant low-voltage warning

SJFOM, 2025-06-27:
Enable smart handling of low voltage so that we aren't constantly notified of a low battery.

Nice to have - disable motor movement if battery is too low

Closed 2025-07-23.

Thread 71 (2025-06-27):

Implement motor motion profile class to handle joystick input modes

SJFOM, 2025-06-27:
An interface layer which takes input (such as joystick values) and outputs velocity values for the `tmc_control` class would futureproof the implementation and improve clarity when working on issues such as #67 and #68

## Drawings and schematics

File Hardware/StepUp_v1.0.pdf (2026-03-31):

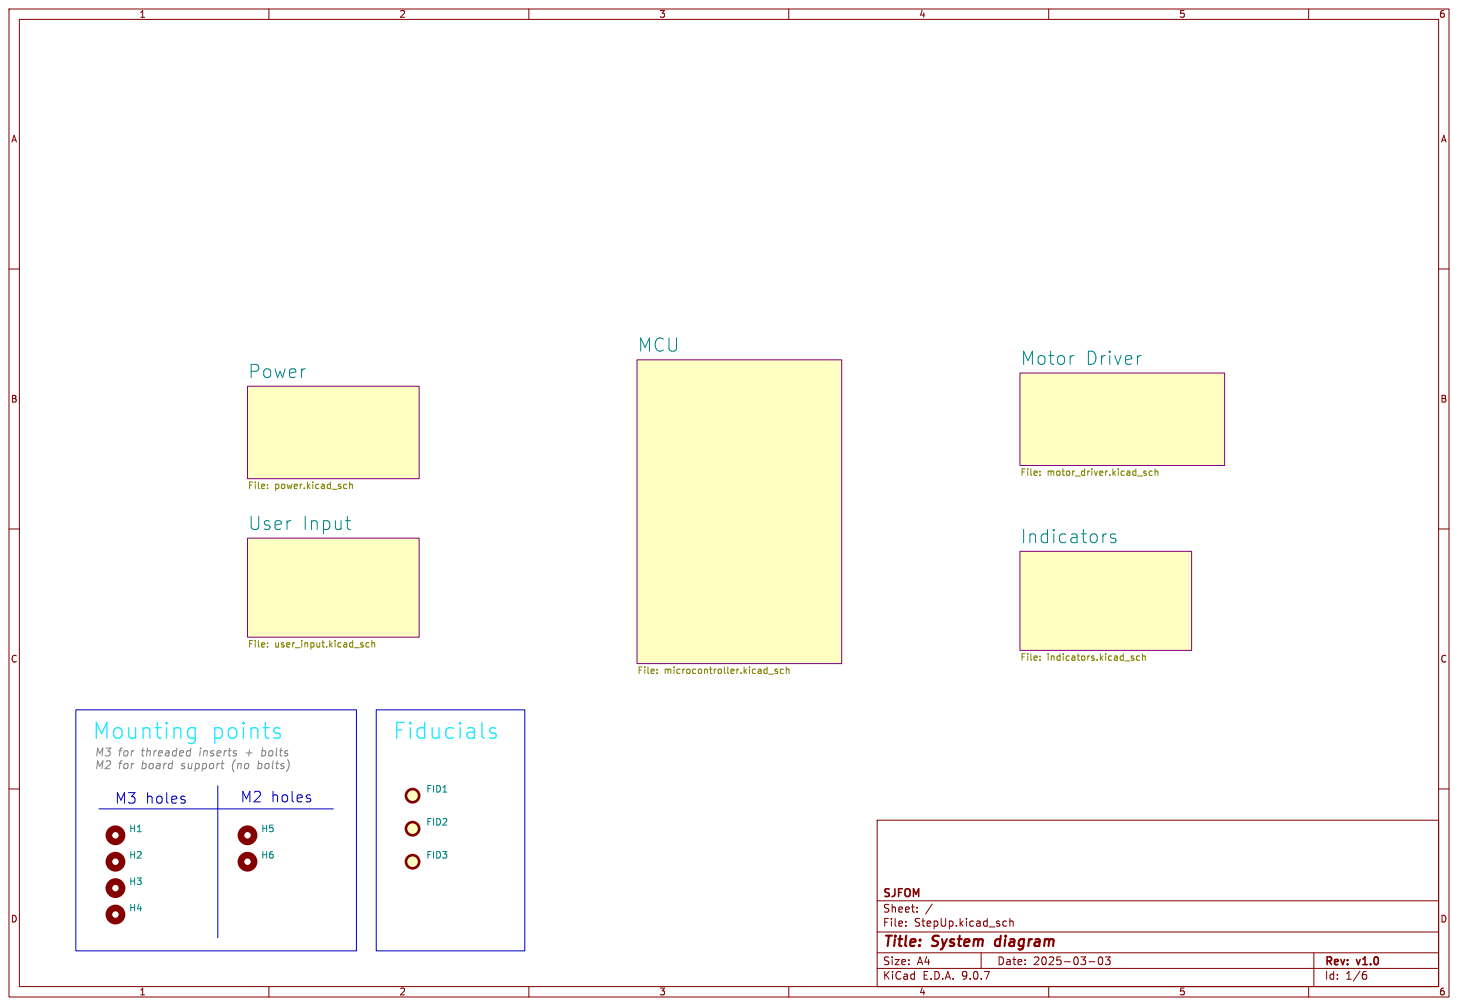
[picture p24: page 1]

File: StepUp.kicad_sch Sheet: / SJFOM Power

M3 for threaded inserts + bolts M2 for board support (no bolts)

Id: 1/6 Title: System diagram

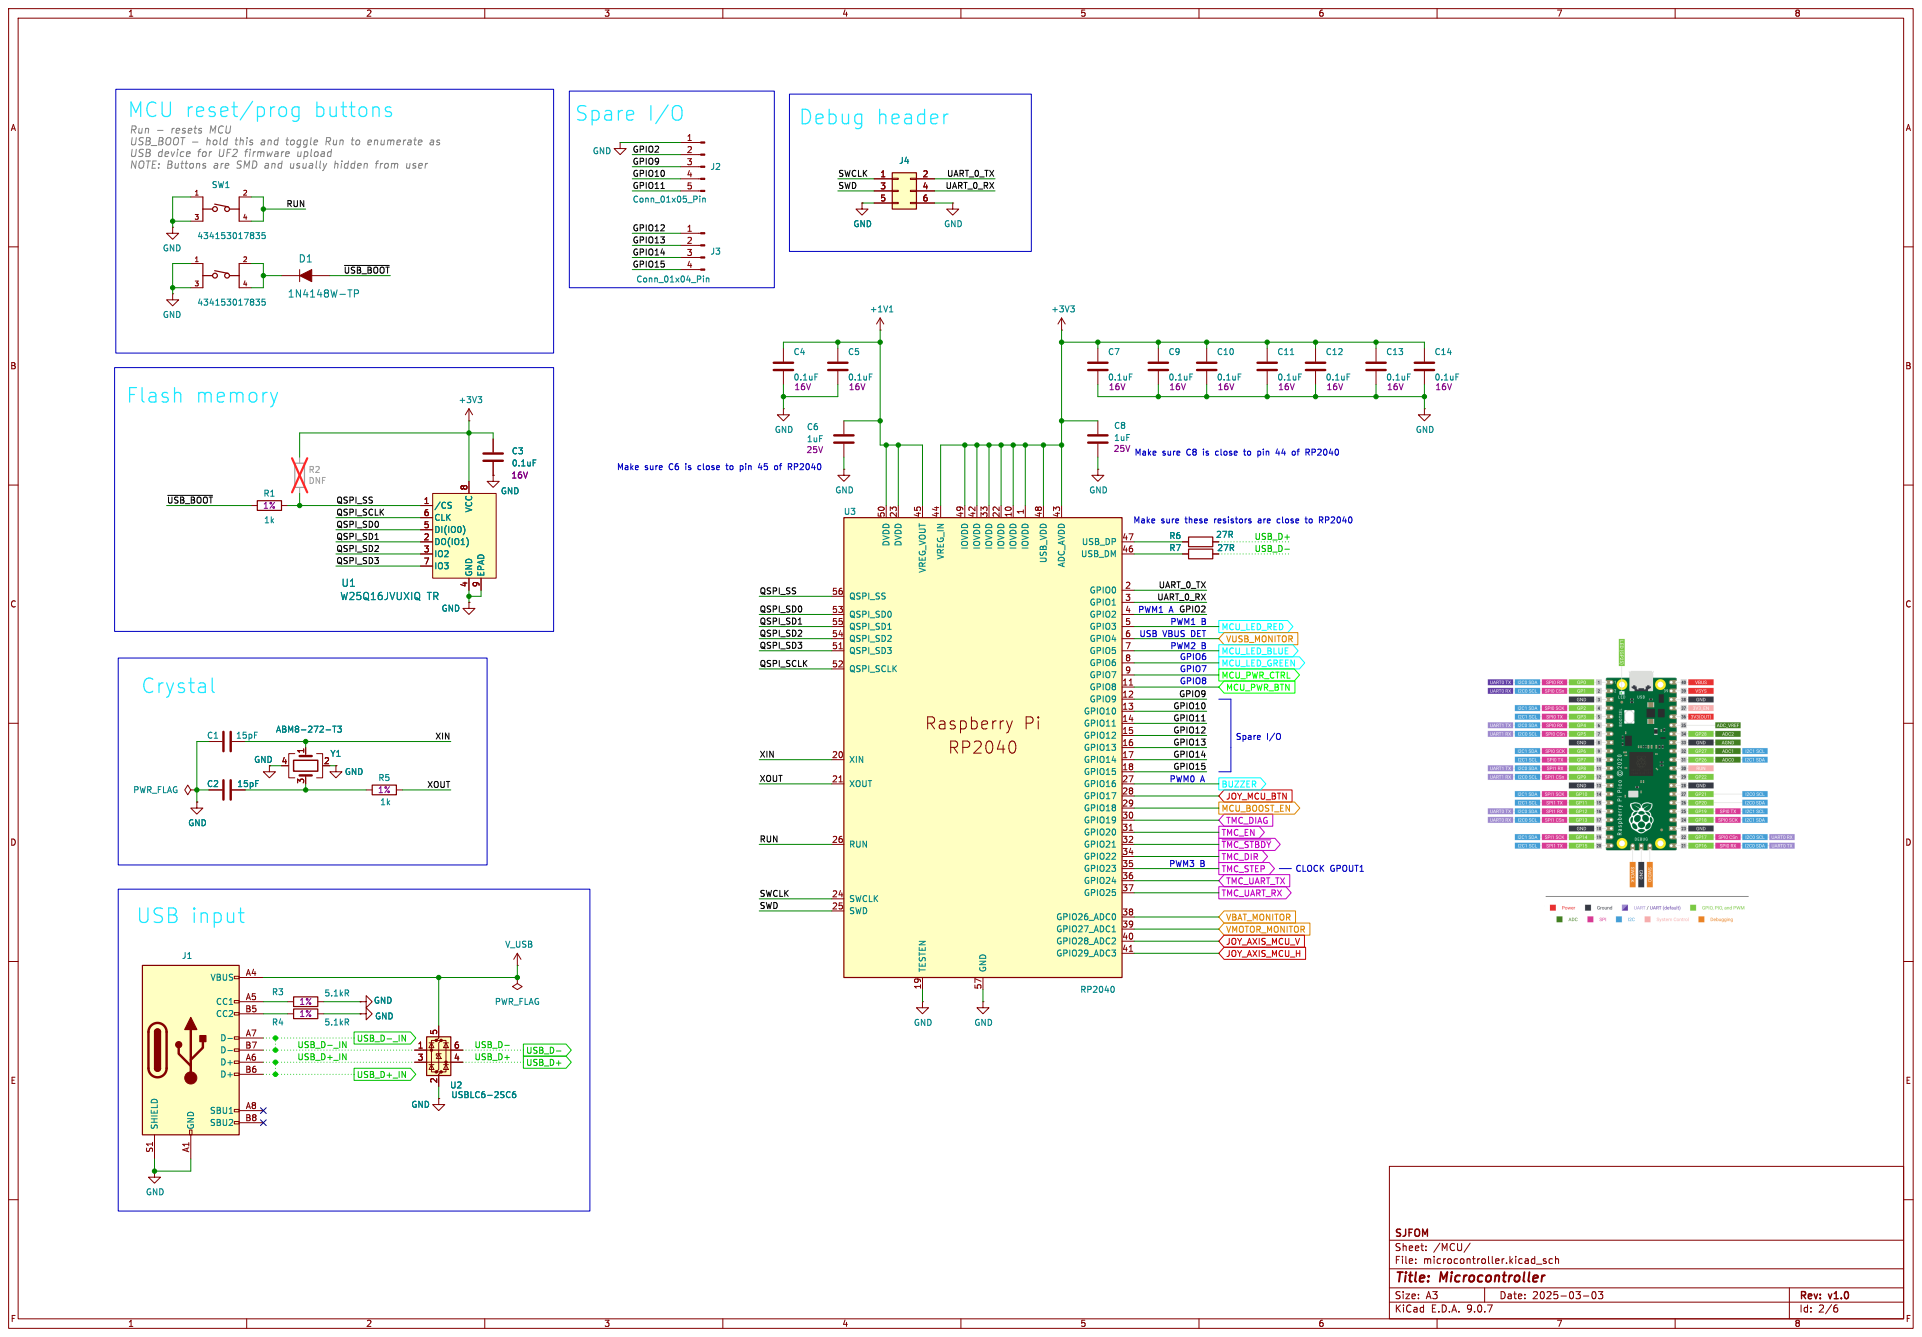
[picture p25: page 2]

USB VBUS DET GPIO6 Debug header

Make sure C8 is close to pin 44 of RP2040 Run - resets MCU

Id: 2/6 Title: Microcontroller File: microcontroller.kicad_sch Sheet: /MCU/ SJFOM

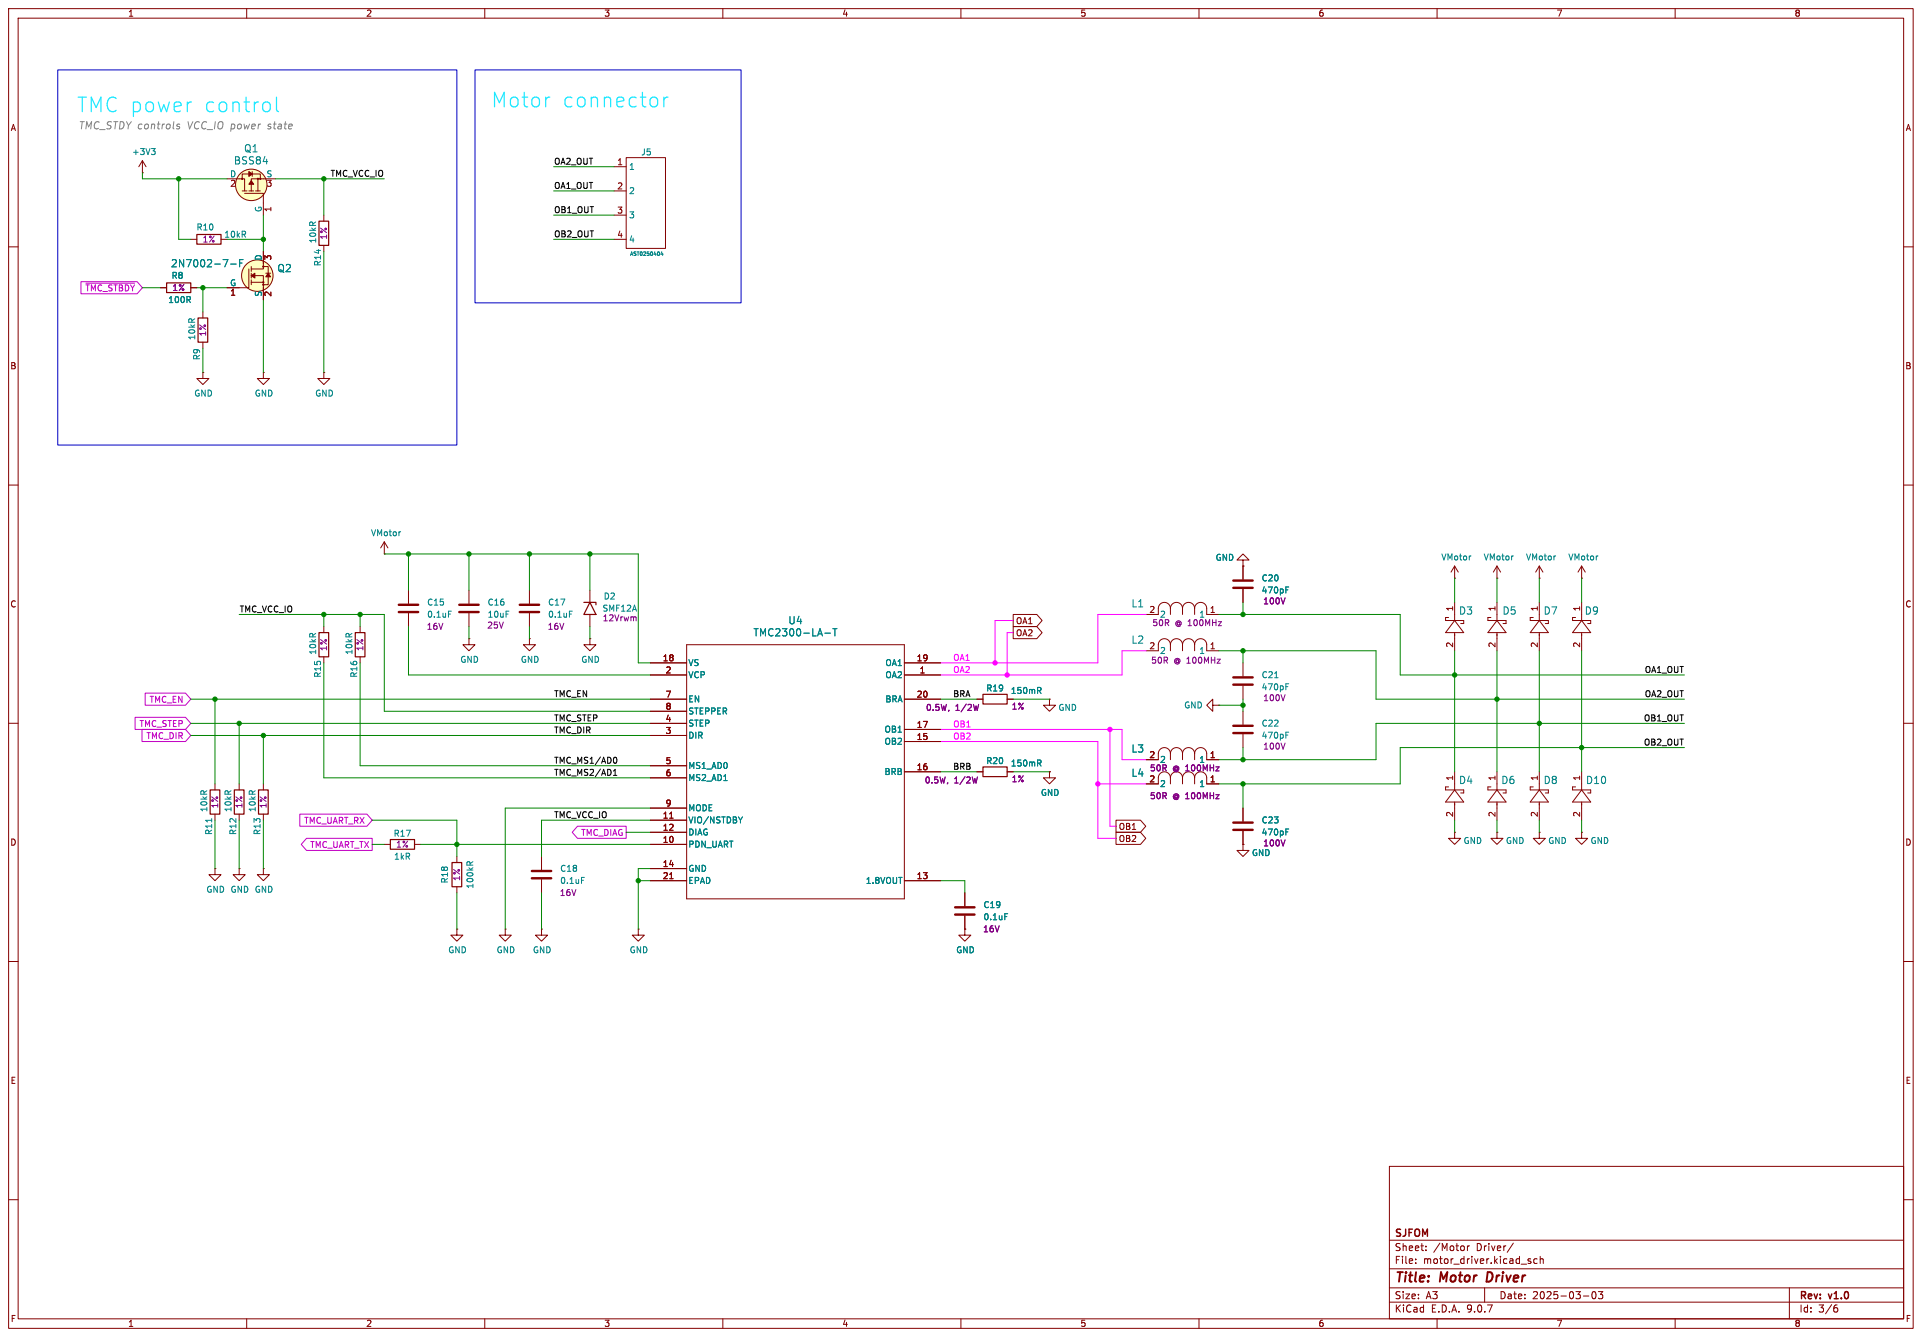
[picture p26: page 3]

2 1D8 GND GND GND GND GND

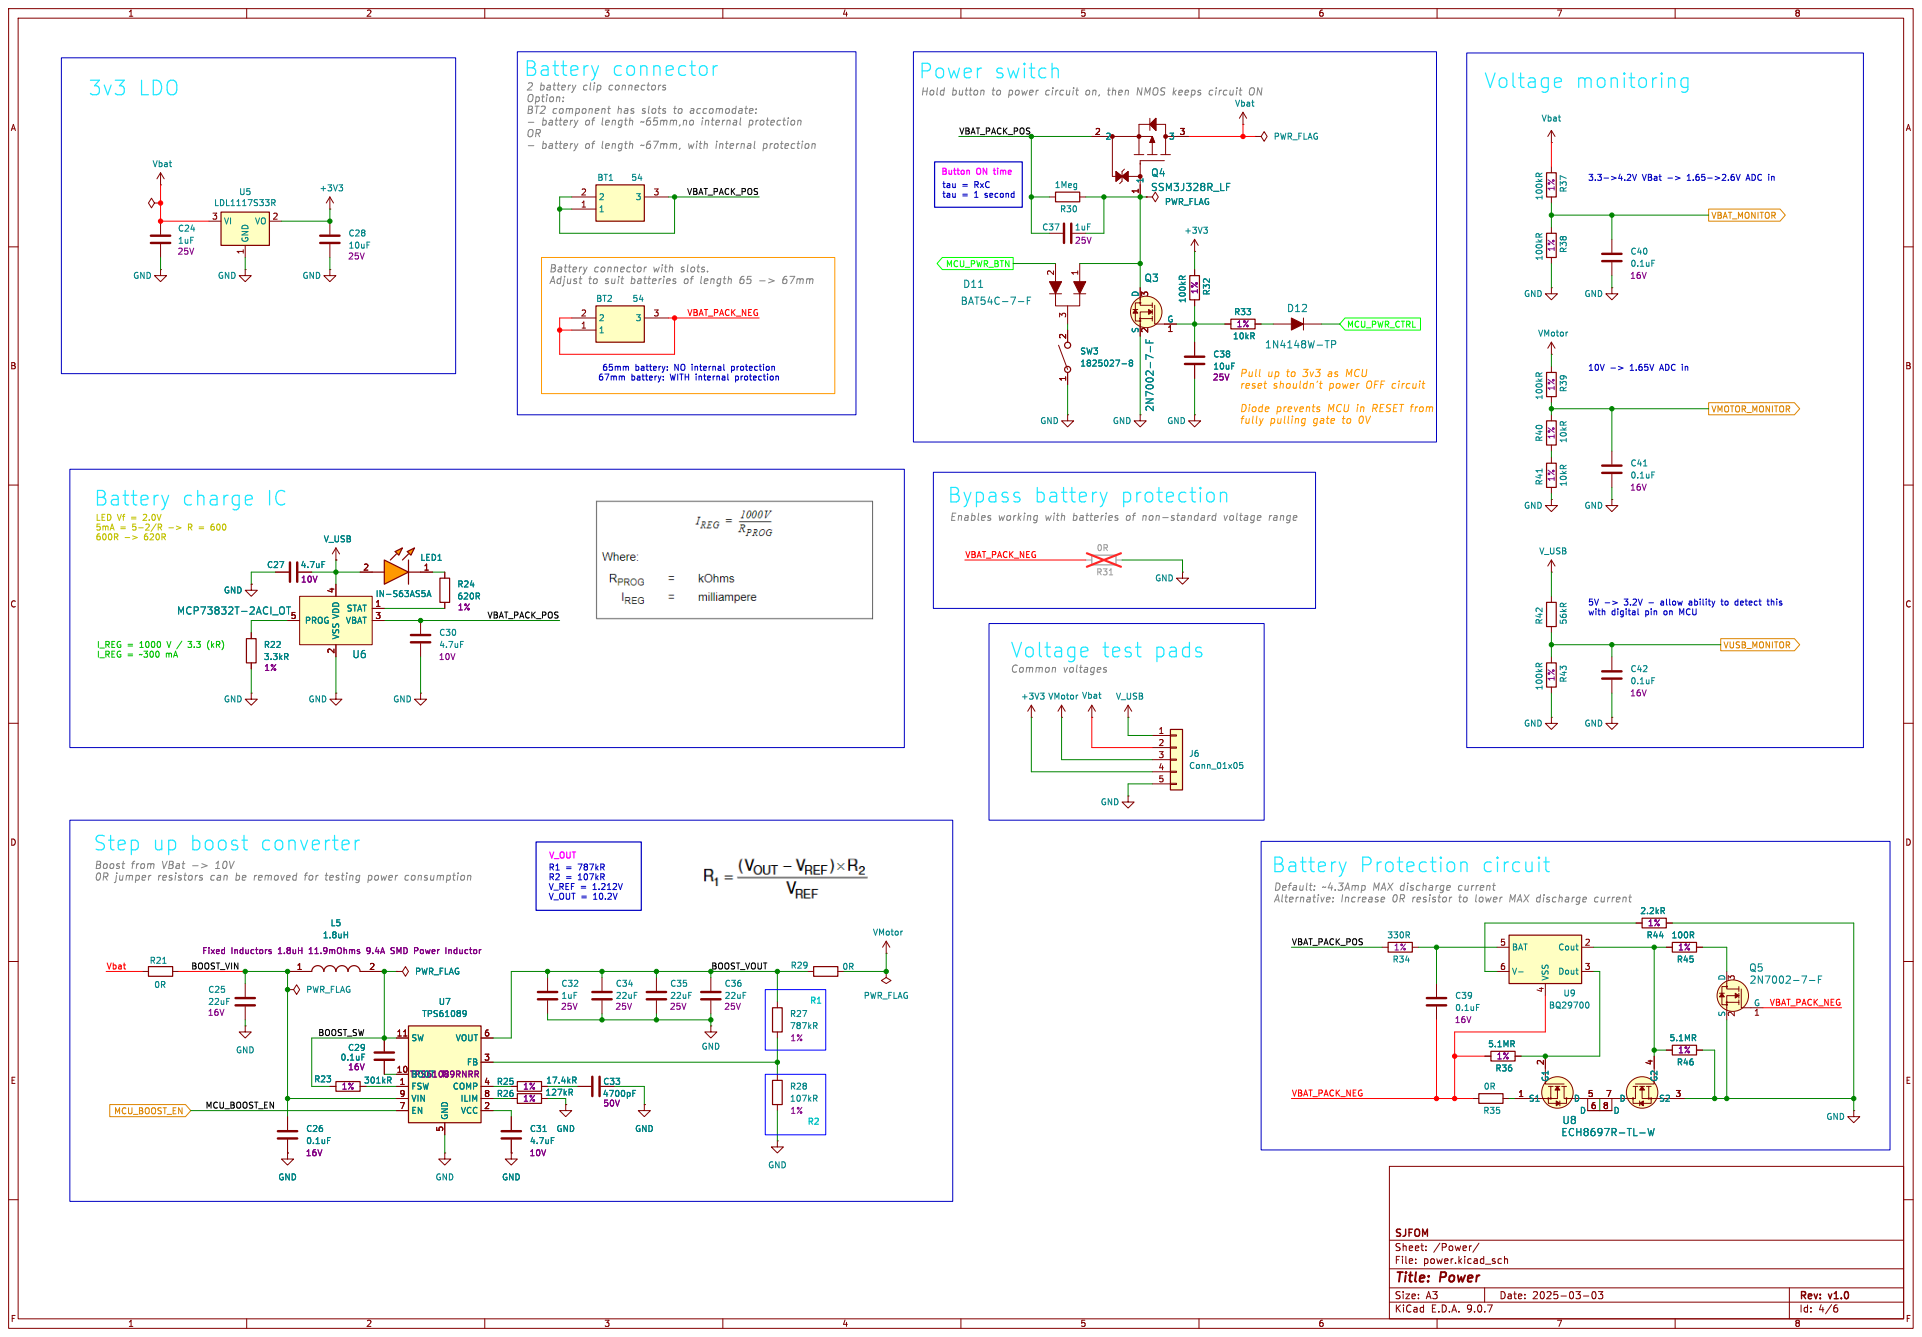
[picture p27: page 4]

Button ON time Battery connector
tau = 1 second Battery charge IC

fully pulling gate to 0V

Id: 4/6 Title: Power File: power.kicad_sch Sheet: /Power/ SJFOM

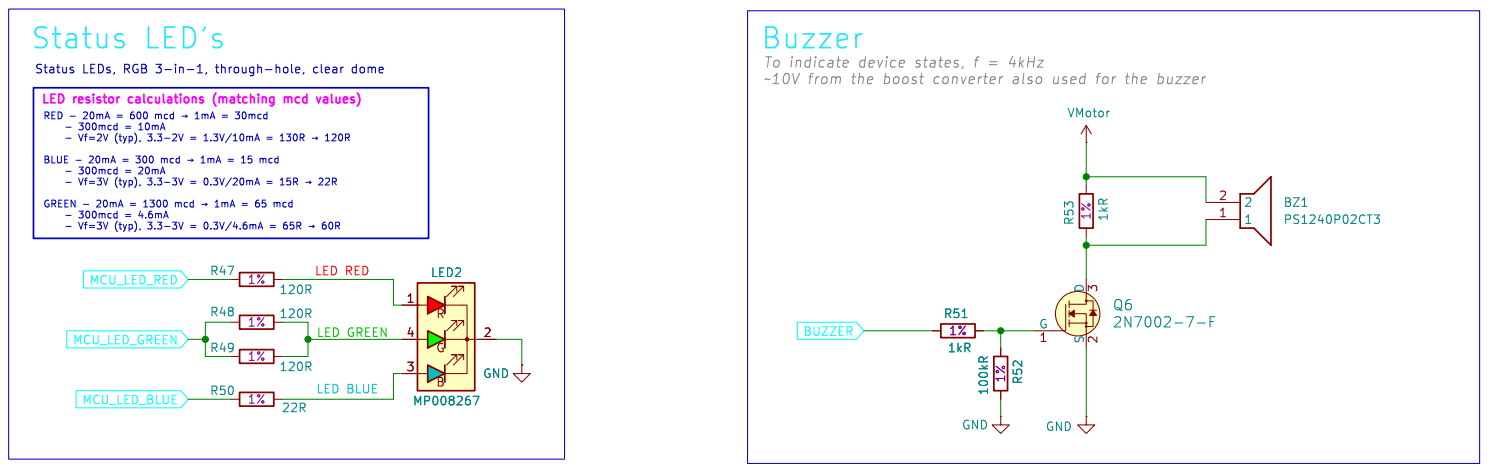
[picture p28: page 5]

BLUE - 20mA = 300 mcd þÿ!’1mA = 15 mcd
- 300mcd = 20mA

Id: 5/6 Title: User Input File: indicators.kicad_sch Sheet: /Indicators/ SJFOM

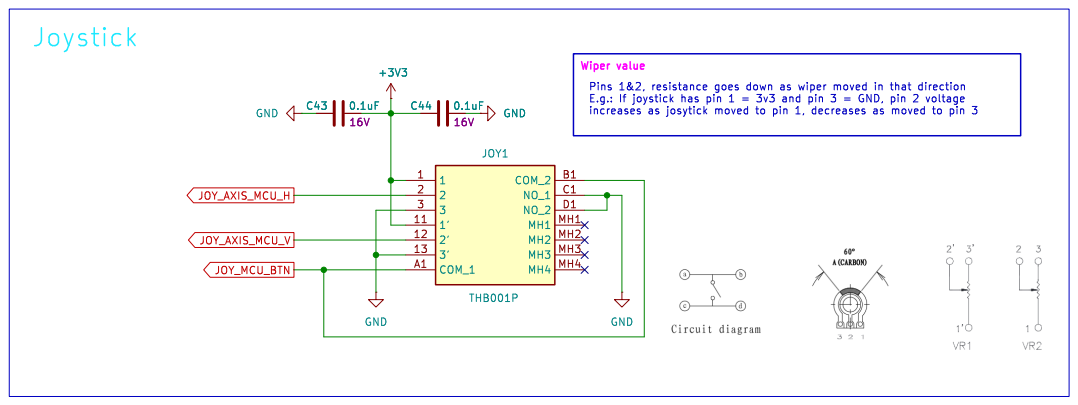
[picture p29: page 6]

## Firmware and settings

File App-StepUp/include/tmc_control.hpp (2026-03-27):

/**
 * @file tmc_control.hpp
 * @author Sam (@SJFOM)
 * @brief
 * @version 0.1
 * @date 2024-09-26
 *
 * @copyright Copyright (c) 2024
 * @license   MIT
 *
 */

#ifndef TMC_CONTROL_H_
#define TMC_CONTROL_H_

// pico-sdk
#include "pico/stdlib.h"  // Includes `hardware_gpio.h`

// Logging utilities
#include "PicoUtils.h"

// Control libraries
#include "ControlInterface.hpp"

// pin includes
#include "board_definitions.h"

// TMC-API
extern "C"
{
#include "../../../Libraries/TMC_API/helpers/CRC.h"
#include "../../../Libraries/TMC_API/helpers/Config.h"
#include "../../../Libraries/TMC_API/ic/TMC2300.h"
}

// PinManager
#include "pin_event_manager.hpp"

// printf can default to using uart0 so use uart1 instead
#define TMC_UART_ID   uart1
#define TMC_BAUD_RATE ((unsigned)460800)

#define TMC_UART_SLAVE_ADDRESS (3U)

#define TMC_UART_CHANNEL (0)  // Not as relevant for single IC use case

// Default motion profile ramp configurations
#define VELOCITY_RAMP_INCREMENT_STEPS_PER_SECOND (500U)
#define VELOCITY_STARTING_STEPS_PER_SECOND       (10000U)

// Rate at which we decrement the velocity if we reach Stallgaurd threshold
// limits
#define VELOCITY_RAMP_SG_LIMIT_DECREMENT_STEPS_PER_SECOND \
    (VELOCITY_RAMP_INCREMENT_STEPS_PER_SECOND * 5U)

// Used for threshold where open-circuit flags are valid - datasheet says they
// are valid for "slow speed" movements
#define VELOCITY_SLOW_SPEED_STEPS_PER_SECOND \
    (2 * VELOCITY_STARTING_STEPS_PER_SECOND)

#define VELOCITY_MAX_STEPS_PER_SECOND (30000U)

// Run and hold current values (0..31U) scaled to 1.2A RMS
#define DEFAULT_IRUN_VALUE  (11U)
#define DEFAULT_IHOLD_VALUE (0U)

// If SG_VALUE falls below 2x SGTHRS_VALUE then a stall detection is triggered
// SG_VALUE = 0..510 (higher number, lighter loading)
// 90% loading = 510 - 0.9*510 = 0.1*510 = 51
// SGTHRS = 51/2 ~= 25
constexpr uint16_t CX_DEFAULT_SGTHRS_VALUE = 25U;

/*****************************/
/* General Registers - START */
/*****************************/
struct GCONF_t
{
    // READ + WRITE register
    constexpr static uint8_t address = TMC2300_GCONF;

    /* GCONF: Global Configuration Flags */
    union
    {
        uint8_t sr;
        struct
        {
            bool : 1, extcap : 1, : 1, shaft : 1, diag_index : 1, diag_step : 1,
                multistep_filt : 1, test_mode : 1;
        };
    };
    // Default constructor holds reset values
    GCONF_t() : extcap(0), multistep_filt(1) {}
};

struct GSTAT_t
{
    // READ + WRITE register, Clear upon WRITE
    constexpr static uint8_t address = TMC2300_GSTAT;

    /* GSTAT: Global Status Flags */
    union
    {
        uint8_t sr : 3;
        struct
        {
            bool reset : 1, drv_err : 1, u3v5 : 1;
        };
    };
};

struct IFCNT_t
{
    // READ only register
    constexpr static uint8_t address = TMC2300_IFCNT;

    /* Interface  transmission  counter.  This  register  becomes incremented
     * with each successful UART interface write access. Read  out  to  check
     * the serial transmission  for lost  data.  Read  accesses  do  not  change
     * the  content. The counter wraps around from 255 to 0.*/
    uint8_t sr;
};

struct SLAVECONF_t
{
    // WRITE only register
    constexpr static uint8_t address = TMC2300_SLAVECONF;
    union
    {
        uint8_t sr;
        struct
        {
            uint8_t : 8;
            uint8_t send_delay_bit_time : 4;
        };
    };
};

struct IOIN_t
{
    // READ only register
    constexpr static uint8_t address = TMC2300_IOIN;

    /* IOIN: INPUT - Reads the state of all input pins available */
    union
    {
        uint32_t sr;
        struct
        {
            bool en : 1, nstdby : 1, ad0 : 1, ad1 : 1, diag : 1, stepper : 1,
                pdn_uart : 1, mode : 1, step : 1, dir : 1, comp_a1a2 : 1,
                comp_b1b2 : 1;
            uint16_t : 12;
            uint8_t version : 8;
        };
    };
};

/***************************/
/* General Registers - END */
/***************************/

/**************************************/
/* Velocity Dependent Control - START */
/**************************************/
struct IHOLD_IRUN_t
{
    // WRITE only register
    constexpr static uint8_t address = TMC2300_IHOLD_IRUN;

    /* IHOLD_IRUN: Driver Current control */

    union
    {
        uint32_t sr : 20;
        struct
        {
            // TODO: Re-order: check the following is now correct
            uint8_t ihold : 5, : 3, irun : 5, : 3, iholddelay : 4;
        };
    };

    // Default constructor holds reset values
    IHOLD_IRUN_t() : ihold(8U), irun(31U), iholddelay(1U) {}
};

struct TPOWERDOWN_t
{
    // WRITE only register
    constexpr static uint8_t address = TMC2300_TPOWERDOWN;

    /* Sets the delay time from stand-still (stst) detection to motor current
     * power down. Time range is about 0 to 5.6 seconds. */
    uint8_t sr : 8;

    // Default constructor holds reset value
    TPOWERDOWN_t() : sr(20U) {}
};

struct TSTEP_t
{
    // READ only register
    constexpr static uint8_t address = TMC2300_TSTEP;

    /* Actual measured time between two 1/256 microsteps derived from the step
     * input frequency in units of 1/fCLK. Measured value is (2^20)-1 in case of
     * overflow or stand still. */
    uint32_t sr : 20;
};

struct VACTUAL_t
{
    // WRITE only register
    constexpr static uint8_t address = TMC2300_VACTUAL;
    int32_t sr : 24;
};

/************************************/
/* Velocity Dependent Control - END */
/************************************/

/******************************/
/* StallGuard Control - START */
/******************************/
struct TCOOLTHRS_t
{
    // WRITE only register
    constexpr static uint8_t address = TMC2300_TCOOLTHRS;

    /* This is the lower threshold velocity for switching on smart energy
     * CoolStep and StallGuard feature. RANGE: 1..2^20-1. DEFAULT: 0 */
    uint32_t sr : 20;
};

struct SGTHRS_t
{
    // WRITE only register
    constexpr static uint8_t address = TMC2300_SGTHRS;

    /* Detection threshold for stall. The StallGuard value SG_VALUE becomes
     * compared to this threshold. */
    uint8_t sr : 8;
};

struct SGVALUE_t
{
    // READ only register
    constexpr static uint8_t address = TMC2300_SG_VALUE;

    /* StallGuard result. SG_RESULT becomes updated with each fullstep,
     * independent of TCOOLTHRS and SGTHRS. A higher value signals a lower motor
     * load and more torque headroom. Intended for StealthChop mode, only. Bits
     * 9 and 0 will always show 0. Scaling to 10 bit is for compatibility to
     * StallGuard2. */
    uint16_t sr : 10;
};

struct COOLCONF_t
{
    // WRITE only register
    constexpr static uint8_t address = TMC2300_COOLCONF;

    /* COOLCONF: Smart energy control CoolStep and StallGuard. DEFAULT: 0
     * (disabled)*/
    union
    {
        uint16_t sr;
        struct
        {
            /* NOTE: semin = 0, smart current control coolStep = OFF */
            // FIXME: This register WORKS if the bit order is backwards to the
            // other registers?.. Look into struct packing, maybe this isn't
            // consistent?
            bool seimin : 1;
            uint8_t sedn : 2, : 1, semax : 4, : 1, seup : 2, : 1, semin : 4;
        };
    };
};

/****************************/
/* StallGuard Control - END */
/****************************/

/*******************************/
/* Sequencer Registers - START */
/*******************************/
struct MSCNT_t
{
    // READ only register
    constexpr static uint8_t address = TMC2300_MSCNT;

    /* Microstep counter. Indicates actual position in the microstep table
     * for CUR_A. CUR_B uses an offset of 256 into the table. Reading out
     * MSCNT allows determination of the motor position within the
     * electrical wave.*/
    union
    {
        uint16_t sr : 10;
    };
};

/*****************************/
/* Sequencer Registers - END */
/*****************************/

/*************************************/
/* Chopper Control Registers - START */
/*************************************/

struct CHOPCONF_t
{
    // READ + WRITE register
    constexpr static uint8_t address = TMC2300_CHOPCONF;

    /* CHOPCONF: Chopper Configuration */
    union
    {
        uint32_t sr;
        struct
        {
            bool enabledrv : 1;
            uint16_t : 14;
            uint8_t tbl : 2, : 7, mres : 4;
            bool intpol : 1, dedge : 1, diss2g : 1, diss2vs : 1;
        };
    };
    // Default constructor holds reset value
    CHOPCONF_t() : sr(0x13008001) {}
};
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

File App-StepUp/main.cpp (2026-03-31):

/**
 * StepUp! main file
 *
 * @copyright 2025, Sam O'Mahony (@SJFOM)
 * @version   0.1
 * @licence   MIT
 *
 */
#include "include/main.h"

#include "pico/async_context_freertos.h"
#include "pico/multicore.h"
#include "task.h"
#if (SERIAL_OVER_USB == 1)
#    include "tusb.h"
#endif

using std::string;
using std::stringstream;
using std::vector;

/*
 * GLOBALS
 */

// Static variables
static bool s_init_complete = false;

// This is the inter-task queue
volatile QueueHandle_t queue_power_control_data = NULL;
volatile QueueHandle_t queue_motor_control_data = NULL;
volatile QueueHandle_t queue_led_notification_task = NULL;
volatile QueueHandle_t queue_buzzer_notification_task = NULL;
volatile QueueHandle_t queue_led_colour_data = NULL;

// Set loop delay times (in ms)
const TickType_t power_control_job_delay_ms = 1000 / portTICK_PERIOD_MS;
const TickType_t joystick_job_delay_ms = 10 / portTICK_PERIOD_MS;
const TickType_t tmc_job_delay_ms = 20 / portTICK_PERIOD_MS;
const TickType_t led_job_delay_ms = 80 / portTICK_PERIOD_MS;
const TickType_t buzzer_job_delay_ms = 100 / portTICK_PERIOD_MS;
const TickType_t voltage_monitoring_job_delay = 1000 / portTICK_PERIOD_MS;
const TickType_t watchdog_job_delay_ms =
    CX_WATCHDOG_CALLBACK_MS / portTICK_PERIOD_MS;

// FROM 1.0.1 Record references to the tasks
TaskHandle_t power_control_task_handle = NULL;
TaskHandle_t joystick_task_handle = NULL;
TaskHandle_t tmc_task_handle = NULL;
TaskHandle_t led_task_handle = NULL;
TaskHandle_t buzzer_task_handle = NULL;
TaskHandle_t voltage_monitoring_task_handle = NULL;

// Task priorities (higher value = higher priority)
UBaseType_t job_priority_power_control = (tskIDLE_PRIORITY + 3U);
UBaseType_t job_priority_joystick_control = (tskIDLE_PRIORITY + 2U);
UBaseType_t job_priority_tmc_control = (tskIDLE_PRIORITY + 2U);
UBaseType_t job_priority_buzzer_control = (tskIDLE_PRIORITY + 1U);
UBaseType_t job_priority_led_control = (tskIDLE_PRIORITY + 1U);
UBaseType_t job_priority_voltage_monitoring = (tskIDLE_PRIORITY + 1U);

// Create class instances of control interfaces
TMCControl tmc_control(CX_R_SENSE, CX_COOLSTEP_ENABLED);
JoystickControl joystick_control;
BuzzerControl buzzer_control(BUZZER_PIN);
LEDControl led_control(LED_PIN_RED, LED_PIN_GREEN, LED_PIN_BLUE);
PowerControl power_control(CX_POWER_BUTTON_OFF_HOLD_TIMEOUT_MS,
                           CX_POWER_DOWN_INACTIVE_TIMEOUT_MS);

// Create voltage monitoring class instances
VoltageMonitoring battery_voltage_monitoring(
    "Battery",
    VBAT_MONITOR_ADC_PIN,
    VBAT_MONITOR_ADC_CHANNEL,
    VBAT_ADC_SCALING_FACTOR,
    CX_BATTERY_VOLTAGE_THRESHOLD_LOW,
    CX_BATTERY_VOLTAGE_THRESHOLD_HIGH,
    CX_BATTERY_VOLTAGE_DELTA_THRESHOLD,
    VoltageBoundsSensitivityState::VOLTAGE_STATE_SENSITIVITY_MEDIUM);

VoltageMonitoring motor_voltage_monitoring(
    "Motor",
    VMOTOR_MONITOR_ADC_PIN,
    VMOTOR_MONITOR_ADC_CHANNEL,
    VMOTOR_ADC_SCALING_FACTOR,
    CX_MOTOR_IDLE_VOLTAGE_THRESHOLD_LOW,
    CX_MOTOR_IDLE_VOLTAGE_THRESHOLD_HIGH,
    CX_BATTERY_VOLTAGE_DELTA_THRESHOLD,
    VoltageBoundsSensitivityState::VOLTAGE_STATE_SENSITIVITY_LOW);

/*
 * SETUP FUNCTIONS
 */

/**
 * @brief Hardware setup routine.
 */
void setup()
{
    setup_watchdog();
    setup_buzzer();
    setup_led();
    setup_tmc2300();
    setup_boost_converter();
    setup_voltage_monitoring();
    setup_joystick();
}

void setup_watchdog()
{
    LOG_INFO("Watchdog setup...");
    if (watchdog_caused_reboot())
    {
        LOG_INFO("Watchdog caused reboot");
    }
    // Enable the watchdog timer
    watchdog_enable(CX_WATCHDOG_TIMEOUT_MS, 1 /*pause_on_debug*/);

    // Set the watchdog timer to reset the system if it is not fed within the
    // specified timeout period
    watchdog_update();

    LOG_INFO("Watchdog setup... OK");
}

void setup_power_control()
{
    LOG_INFO("Power control setup...");
    if (power_control.init())
    {
        LOG_INFO("Power control setup... OK");
    }
    else
    {
        LOG_ERROR("Power control setup... FAIL");
    }

    if (power_control.isUSBInserted())
    {
        LOG_INFO("USB cable detected");
    }
}

/**
 * @brief Set the up TMC2300 IC
 *
 * @details Configure UART, power on IC, reset register state to defaults,
 * verify silicon version
 *
 */
void setup_tmc2300()
{
    LOG_INFO("TMC2300 setup...");

    bool tmc_setup_success = true;
    // If this fails on a call to writing to TMC then it will be blocking!
    tmc_setup_success &= tmc_control.init();

    if (tmc_control.getChipID() == TMC2300_VERSION_COMPATIBLE)
    {
        LOG_INFO("TMC2300 silicon version: 0x40");
    }
    else
    {
        LOG_WARN("TMC version: UNSUPPORTED!");
        tmc_setup_success = false;
    }

    // Send configuration to TMC2300 - this is needed to set up the UART and put
    // the IC into a known state.
    LOG_INFO("Configure TMC2300 default values...");
    tmc_control.defaultConfiguration();
    LOG_INFO("Configure TMC2300 default values - OK!");

    if (tmc_setup_success)
    {
        LOG_INFO("TMC2300 setup... OK");
    }
    else
    {
        LOG_ERROR("TMC2300 setup... FAIL");
    }
}

void setup_boost_converter()
{
    LOG_INFO("Boost converter setup...");

    // Enable boost converter pin control
    gpio_init(TMC_PIN_BOOST_EN);
    gpio_set_dir(TMC_PIN_BOOST_EN, GPIO_OUT);

    // Enable boost converter
    gpio_put(TMC_PIN_BOOST_EN, 1);

    LOG_INFO("Boost converter setup... OK");
}

/**
 * @brief Set the up joystick object
 *
 */
void setup_joystick()
{
    LOG_INFO("Joystick setup...");

    if (joystick_control.init())
    {
        joystick_control.enableFunctionality(true);
    }
    else
    {
        // This will be true if no joystick present OR the josytick is not
        // centered
        LOG_ERROR("Joystick setup... FAIL");
    }
    LOG_INFO("Joystick setup... OK");
}

void setup_buzzer()
{
    LOG_INFO("Buzzer setup...");
    if (buzzer_control.init())
    {
        buzzer_control.enableFunctionality(true);
        buzzer_control.setBuzzerFunction(ControllerNotification::NOTIFY_BOOT);
    }
    else
    {
        // FIXME: When will this ever be true?
        LOG_ERROR("Buzzer setup... FAIL");
    }
    LOG_INFO("Buzzer setup... OK");
}

void setup_led()
{
    LOG_INFO("LED setup...");
    if (led_control.init())
    {
        led_control.enableFunctionality(true);
        led_control.setLEDFunction(ControllerNotification::NOTIFY_BOOT);
    }
    else
    {
        // FIXME: When will this ever be true?
        LOG_ERROR("LED setup... FAIL");
    }
    LOG_INFO("LED setup... OK");
}

void setup_voltage_monitoring()
{
    LOG_INFO("Voltage monitoring setup...");
    if (battery_voltage_monitoring.init())
    {
        battery_voltage_monitoring.enableFunctionality(true);
        LOG_INFO("Battery voltage monitoring setup... OK");
    }
    else
    {
        LOG_ERROR("Battery voltage monitoring setup... FAIL");
    }

    // NOTE: This may fail if we do not initialise the boost converter before
    // now
    if (motor_voltage_monitoring.init())
    {
        motor_voltage_monitoring.enableFunctionality(true);

        // Now we know the motor voltage is in spec, we can broaden the expected
        // motor voltage range to accommodate the back-emf generated by a
        // spinning motor (10% bounds)
        motor_voltage_monitoring.setVoltageThresholds(
            CX_MOTOR_ACTIVE_VOLTAGE_THRESHOLD_LOW,
            CX_MOTOR_ACTIVE_VOLTAGE_THRESHOLD_HIGH);
        LOG_INFO("Boost/Motor voltage monitoring setup... OK");
    }
    else
    {
        LOG_ERROR("Boost/Motor voltage monitoring setup... FAIL");
    }

    LOG_INFO("Voltage monitoring setup...OK");
}

/*
 * CORE 1 USB SERVICE
 */

/**
 * @brief USB service function - runs on core 1 to service TinyUSB events
 * @details This function runs on core 1 to keep USB responsive while
 * core 0 (running FreeRTOS) executes application tasks with blocking I/O (e.g.
 * TMC UART setup) Launched via multicore_launch_core1() before scheduler
 * starts.
 */
#if (SERIAL_OVER_USB == 1)
void core1_usb_service()
{
    tusb_init();
    while (true)
    {
        // Service TinyUSB device task on core 1
        // NOTE: Both core0 (async context) and core1 may call this, but
        // tud_task() handles concurrent calls gracefully through its internal
        // state management
        tud_task();
    }
}
#endif
/*
 * TASK FUNCTIONS
 */

/**
 * @brief Process tasks on the TMC2300 motor controller IC
 */
[[noreturn]] void tmc_process_job(void *unused_arg)
{
    enum ControllerNotification tmc_notify =
        ControllerNotification::NOTIFY_BOOT;
    ControllerState tmc_state = ControllerState::STATE_IDLE;
    TMCData tmc_data = {};

    while (true)
    {
        vTaskDelay(tmc_job_delay_ms);

        tmc_state = tmc_control.processJob(xTaskGetTickCount());

        switch (tmc_state)
        {
            case ControllerState::STATE_IDLE:
            {
                // Only fall here if peripheral not yet initialised
                break;
            }
            case ControllerState::STATE_READY:
            {
                static MotorControlData motor_data = {};
                // Check for an item in the FreeRTOS xQueue
                if (xQueueReceive(queue_motor_control_data, &motor_data, 0) ==
                    pdPASS)
                {
                    if (motor_data.button_press)
                    {
                        LOG_INFO("Button press - stopping motor!");
                        // A button press event should instantly stop the
                        // motor
                        tmc_control.resetMovementDynamics();
                    }
                    else
                    {
                        tmc_control.updateMovementDynamics(
                            motor_data.velocity_delta,
                            motor_data.direction);
                    }
                }
                break;
            }
            case ControllerState::STATE_NEW_DATA:
            {
                // tmc_control get State
                tmc_data = tmc_control.getTMCData();

                if (false == tmc_data.diag.normal_operation)
                {
                    // Most likely case is to emit a WARN signal if we enter
                    // this state
                    tmc_notify = ControllerNotification::NOTIFY_WARN;
                    bool trigger_led = true;
                    bool trigger_buzzer = true;

                    if (tmc_data.diag.stall_detected)
                    {
                        LOG_DEBUG("Stall detected!");
                        // Don't trigger a typical info or warn message as
                        // we don't need to alert to the user that a max rpm
                        // has been reached as this will likely happen very
                        // often
                        trigger_led = false;
                        trigger_buzzer = false;

                        tmc_notify = ControllerNotification::NOTIFY_DATA;

                        enum LEDColourNames led_colour =
                            LEDColourNames::LED_COLOUR_WHITE;
                        xQueueSendToBack(queue_led_colour_data, &led_colour, 0);
                    }
                    if (tmc_data.diag.open_circuit ||
                        tmc_data.open_circuit_detected)
                    {
                        // Open circuit detected, trigger a notification
                        tmc_notify = ControllerNotification::NOTIFY_ERROR;
                        LOG_DEBUG("Open circuit detected!");
                        tmc_control.enableFunctionality(false);
                    }
                    if (tmc_data.diag.overheating)
                    {
                        // Overheat event warrants a more assertive
                        // notification to the user
                        tmc_notify = ControllerNotification::NOTIFY_ERROR;
                        LOG_DEBUG("Overheating!");
                        tmc_control.enableFunctionality(false);
                    }
                    if (tmc_data.diag.short_circuit)
                    {
                        LOG_DEBUG("Short circuit detected!");
                    }

                    if (trigger_led)
                    {
                        xQueueSendToBack(queue_led_notification_task,
                                         &tmc_notify,
                                         0);
                    }
                    if (trigger_buzzer)
                    {
                        xQueueSendToBack(queue_buzzer_notification_task,
                                         &tmc_notify,
                                         0);
                    }
                }
                break;
            }
            case ControllerState::STATE_BUSY:
            default:
                // Wait until the tmc2300 is configured
                break;
        }
    }
}
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
int main()
{
    // First set up the hardware so power control can keep PCB powered ON
    setup_power_control();

// Enable either STDIO (UART) or USB (don't enable both)
// Note: USB is initialized on core 1 in core1_usb_service()
#if (SERIAL_OVER_USB == 1)
    stdio_usb_init();
    // Launch USB service on core 1 before scheduler starts
    // This keeps USB responsive while core 0 (FreeRTOS) runs application tasks
    // NOTE: The async context (pico/async_context_freertos.h) may also call
    // tud_task() so we use a spinlock to protect against concurrent access from
    // both core0 and core1
    multicore_launch_core1(core1_usb_service);
#else
    stdio_init_all();
#endif

    sleep_ms(2000);

    // Log app info
    Utils::log_device_info();

    LOG_INFO("Setting up peripherals...");
    setup();
    LOG_INFO("Setting up peripherals... OK!");

    // Create a FreeRTOS timer with a period slightly shorter than the watchdog
    // timeout
    TimerHandle_t timer_watchdog_service =
        xTimerCreate("WatchdogTimer",           // Timer name
                     watchdog_job_delay_ms,     // Timer period in ticks
                     pdTRUE,                    // Auto-reload timer
                     (void *)0,                 // Timer ID (not used here)
                     watchdog_timer_callback);  // Callback function

    if (timer_watchdog_service == NULL)
    {
        LOG_ERROR("Failed to create FreeRTOS timer!");
    }
    else
    {
        if (xTimerStart(timer_watchdog_service, 0) != pdPASS)
        {
            LOG_ERROR("Failed to start FreeRTOS timer!");
        }
        else
        {
            LOG_INFO("FreeRTOS timer started successfully!");
        }
    }

    // FROM 1.0.1 Store handles referencing the tasks; get return values
    // NOTE Arg 3 is the stack depth -- in words, not bytes
    BaseType_t led_status = xTaskCreate(led_process_job,
                                        "GPIO_LED_TASK",
                                        256,
                                        NULL,
                                        job_priority_led_control,
                                        &led_task_handle);
    BaseType_t tmc_status = xTaskCreate(tmc_process_job,
                                        "TMC_JOB_TASK",
                                        256,
                                        NULL,
                                        job_priority_tmc_control,
                                        &tmc_task_handle);
    BaseType_t joystick_status = xTaskCreate(joystick_process_job,
                                             "JOYSTICK_JOB_TASK",
                                             512,
                                             NULL,
                                             job_priority_joystick_control,
                                             &joystick_task_handle);

    BaseType_t buzzer_status = xTaskCreate(buzzer_process_job,
                                           "BUZZER_JOB_TASK",
                                           256,
                                           NULL,
                                           job_priority_buzzer_control,
                                           &buzzer_task_handle);

    BaseType_t voltage_monitoring_status =
        xTaskCreate(voltage_monitoring_process_job,
                    "VOLTAGE_MONITORING_JOB_TASK",
                    256,
                    NULL,
                    job_priority_voltage_monitoring,
                    &voltage_monitoring_task_handle);

    BaseType_t power_control_status = xTaskCreate(power_control_process_job,
                                                  "POWER_CONTROL_JOB_TASK",
                                                  256,
                                                  NULL,
                                                  job_priority_power_control,
                                                  &power_control_task_handle);

    // Set up the event queue
    queue_motor_control_data = xQueueCreate(2, sizeof(struct MotorControlData));
    queue_led_notification_task =
        xQueueCreate(1, sizeof(enum ControllerNotification));
    queue_buzzer_notification_task =
        xQueueCreate(1, sizeof(enum ControllerNotification));
    queue_led_colour_data = xQueueCreate(1, sizeof(LEDColourNames));
    queue_power_control_data =
        xQueueCreate(1, sizeof(enum ControllerNotification));

    // Start the FreeRTOS scheduler if all tasks are created successfully
    if (led_status == pdPASS && tmc_status == pdPASS &&
        joystick_status == pdPASS && buzzer_status == pdPASS &&
        voltage_monitoring_status == pdPASS && power_control_status == pdPASS)
    {
        s_init_complete = true;
        vTaskStartScheduler();
    }

    // We should never get here, but just in case...
    while (true)
    {
        // NOP
    }
}

// Callback function for the repeating timer
void watchdog_timer_callback(__unused TimerHandle_t xTimer)
{
    watchdog_update();  // Feed the watchdog timer
}

extern "C" void on_error_handler(const char *msg)
{
    // Your custom error handling
    printf("[ERROR] Custom error handler: %s\n", msg);
    printf("[WARN] Disabling Watchdog to avoid boot-looping\n");

    watchdog_disable();

    // Critical failure, just turn on red LED if we can and halt
    printf(
        "[ERROR] Critical failure %s init, halting with buzzer and red "
        "LED ON for 5 seconds -> then solid red LED ON.\n",
        s_init_complete ? "post" : "during");

    // Disable other LED pins, just want RED
    gpio_deinit(LED_PIN_BLUE);
    gpio_deinit(LED_PIN_GREEN);

    // Set up red LED pin and turn it on
    gpio_init(LED_PIN_RED);
    gpio_set_dir(LED_PIN_RED, GPIO_OUT);

    gpio_init(BUZZER_PIN);
    gpio_set_dir(BUZZER_PIN, GPIO_OUT);

    // Manual approach to both sounding the buzzer and blinking the LED for
    // ~5 seconds (400us * 12500 iterations = 5s) before halting in an
    // infinite loop.
    for (int i = 0; i < 12500; i++)
    {
        if (i % 1000 == 0)
        {
            gpio_put(LED_PIN_RED, !gpio_get(LED_PIN_RED));
        }
        gpio_put(BUZZER_PIN, 1);
        sleep_us(200);
        gpio_put(BUZZER_PIN, 0);
        sleep_us(200);
    }
    while (true)
    {
        /* Hang in infinite loop - land here if debugging and debugger
             connected*/
        __breakpoint();
    }
}

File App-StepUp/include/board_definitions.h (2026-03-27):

/**
 * @file board_definitions.hpp
 * @author Sam (@SJFOM)
 * @brief ...
 * @version 0.1
 * @date 2025-04-17
 *
 * @copyright Copyright (c) 2025
 * @license MIT
 */

#ifndef BOARD_DEFINITION_H_
#define BOARD_DEFINITION_H_

/**************************/
/* TMC2300 config - START */
/**************************/

// Sense resistor value in Ohms - used for current calculations
constexpr float CX_R_SENSE = (0.15f);

// When we have changed the motor velocity up or down and then stopped the
// motor, the device will remember what speed it got to and ramp its velocity
// towards that previous target speed. Setting this flag to true enables that
// functionality (default = true).
constexpr bool CX_RESUME_PREVIOUS_VELOCITY_ENABLED = true;

// CoolStep automatically reduces the motor current when it detects that the
// motor is not under load, which can help to reduce power consumption and heat
// generation. However, it can also lead to reduced performance in some cases,
// so it is disabled by default.
constexpr bool CX_COOLSTEP_ENABLED = true;

// Experimental: This is not a robust feature for all motor types and should be
// used with caution
// NOTE: This feature will only function if CoolStep is enabled, as it relies on
// the SG_VALUE to determine when to reduce the velocity
constexpr bool CX_HIGH_SPEED_AUTO_REDUCTION_ENABLED = false;

/************************/
/* TMC2300 config - END */
/************************/

/******************************/
/* Power control pins - START */
/******************************/
#define MCU_PWR_CTRL_PIN (7U)
#define MCU_PWR_BTN_PIN  (8U)

/****************************/
/* Power control pins - END */
/****************************/

/***********************/
/* Status pins - START */
/***********************/

#if PCB_REVISION == 1U
#    define LED_PIN_RED   (2U)  // PWM1_A
#    define LED_PIN_GREEN (3U)  // PWM1_B
#    define LED_PIN_BLUE  (5U)  // PWM2_B
#elif PCB_REVISION >= 2U
#    define LED_PIN_RED   (3U)  // PWM1_B
#    define LED_PIN_GREEN (6U)  // Unsure if assigned to any PWM...
#    define LED_PIN_BLUE  (5U)  // PWM2_B
#else
#    error "No valid PCB version found!!"
#endif

#define BUZZER_PIN (16U)  // PWM0_A

/*********************/
/* Status pins - END */
/*********************/

/************************/
/* TMC2300 pins - START */
/************************/

// We are using pins 0 and 1, but see the GPIO function select table in the
// datasheet for information on which other pins can be used.
#define TMC_PIN_UART_TX (25U)
#define TMC_PIN_UART_RX (24U)

// Motor control pins
#define TMC_PIN_ENABLE    (20U)
#define TMC_PIN_N_STANDBY (21U)

// Diagnostics pins
#define TMC_PIN_DIAG (19U)

#define TMC_PIN_BOOST_EN (18U)

// STEP/DIR pins
#define TMC_PIN_STEP (23U)  // PWM3_B
#define TMC_PIN_DIR  (22U)

/**********************/
/* TMC2300 pins - END */
/**********************/

/********************************/
/* Voltage monitor pins - START */
/********************************/

#define VMOTOR_ADC_SCALING_FACTOR (6U)
#define VBAT_ADC_SCALING_FACTOR   (2U)

#define VBAT_MONITOR_ADC_PIN       (26U)
#define VBAT_MONITOR_ADC_CHANNEL   (0)
#define VMOTOR_MONITOR_ADC_PIN     (27U)
#define VMOTOR_MONITOR_ADC_CHANNEL (1U)

#define VUSB_MONITOR_PIN (4U)  // USB_VBUS_DET

/******************************/
/* Voltage monitor pins - END */
/******************************/

/*****************************************/
/* Voltage threshold definitions - START */
/*****************************************/

// N.B: We CANNOT measure voltages below 3.3V with the ADC as the ADC reference
// voltage is also 3.3V. We would need an external reference voltage to measure
// voltages below this threshold.
constexpr float CX_BATTERY_VOLTAGE_THRESHOLD_LOW = 3.4f;
constexpr float CX_BATTERY_VOLTAGE_THRESHOLD_MID_LOW = 3.6f;
constexpr float CX_BATTERY_VOLTAGE_THRESHOLD_MID_HIGH = 3.8f;
constexpr float CX_BATTERY_VOLTAGE_THRESHOLD_HIGH = 4.3f;
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

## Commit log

2022-12-22 feat(template): App now builds -> C++
    Includes TMC2300 header files from previous StepUp Project on ESP32. Not
    tested on real hardware yet.
2023-02-06 wip(uart): Added UART example code
    Will need to move this into TMC2300 library.
2023-02-11 chore(vscode): Workspace ignores other repos
    VSCode should now only present changes to the StepUp-Pico project rather
    than other included submodules (pico-sdk, tinyusb, etc..).
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2023-02-12 feat(uart): Setup & extern methods implemented
2023-02-12 feat(uart): Integrating with main.cpp
2023-02-13 feat(eval): Interfacing with TMC2300-EVAL
    Unsure if UART working as expected, if pinout correct or if channel
    correct. Lots still to work through.
    [tmc_control.cpp]
2023-02-19 feat(uart): Some comms - needs debug
2023-02-19 feat(comms): Pin control + debugging tools
2023-02-27 feat(debug): Now working!!! 🎉
2023-03-04 feat(debug): Added is alive blink LED
2023-03-13 feat(uart): It works!!! 🥳
2023-03-15 feat(debug): Debug Probe working well!
    Now with simple script to upload + monitor with UART from Debug Probe.
2023-03-17 feat(uart): Working well, clean implementation
2023-03-19 chore(uart): Empty commit for PR
2023-04-10 fix(tmc2300): Header file fixes
    [tmc_control.hpp]
2023-04-10 feat(uart): Default config in place
2023-04-15 feat(motor): Motor spinning!!
    DefaultConfig is working, motor tested spinning at various speeds.
2023-04-19 feat(joystick): ADC init & read code
2023-04-23 feat(joystick): Initial working implementation!
    X+ axis has control over motor with 4 levels of speed controllable based
    on X-channel displacement.
2023-05-13 feat(rtos): New structure working!
    Motors spinning, joystick messages passing through to TMC controller.
2023-05-13 feat(led): LED for TMC task now blinks correctly
    [joystick_control.cpp, main.cpp]
2023-05-13 feat(joystick): X&Y separate functions
    X for motor speed + direction, Y for motor current.
2023-07-15 feat(tests): Add sample library with GTEST/MOCK
    Given there's likely more value in testing + mocking library
    functionality vs pin hardware states with the Pico, its valuable to put
    a template for such a library in place now.
2023-10-08 feat(debug): Now runs with v1.5.1 Pico SDK
2023-10-15 fix(control): Motor low speed operation
    [joystick_control.cpp, main.cpp, pins_definitions.h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]
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2023-10-21 feat(diag): Motor move flags working well
    Overtemperature not yet tested - TBD
2023-10-25 wip(irq): Both interrupts working
2023-10-25 feat(button): Debounce working well
2023-10-30 wip(ramp): Several bugs, sort-of works
    [tmc_control.cpp, tmc_control.hpp]
2023-11-19 feat(ramp): Ramp working well
    Need to address decline from initial velocity to lower velocity.
2023-11-19 refactor(ramp): Pushing changes missed in PR
    [tmc_control.cpp]
2024-01-27 wip(stallgaurd): Testing functionality
2024-06-26 feat(pcb): Pinout updates, board worksgcngcn
2024-09-02 fix(tmc): IHOLD reg definition
    [tmc_control.hpp]
2024-09-23 chore(adc): Move generic ADC defs to utils.h
2024-09-23 wip(boost): ADC reads need work...
2024-09-24 feat(adc): Boost voltage working, joy adc settling
2024-09-25 feat(buzzer): First pass working well
    [buzzer_control.cpp, buzzer_control.hpp, main.cpp]
2024-09-26 feat(buzzer): Melody implementation wip
    [buzzer_control.cpp, buzzer_control.hpp]
2024-09-27 feat(buzz): Library working from main loop!
    [buzzer_control.cpp, buzzer_control.hpp, main.cpp]
2024-09-28 feat(buzzer): Warn and Error buzzer melodies
    [buzzer_control.cpp, buzzer_control.hpp]
2024-09-28 feat(buzzer): Button press calls buzzer from main!
    State handling of notifications now part of the ControlInterface
    class and inhereted by each controller.
    [buzzer_control.cpp, buzzer_control.hpp, main.cpp]
2024-09-29 feat(led): Control logic for LED
2024-09-30 fix(buzzer): Working again, task priorities update
    [main.cpp]
2024-09-30 chore(led): Remove redundant comment
2024-10-02 feat(velocity): PWM_SCALE_SUM gates motor velocity
2024-10-02 chore(diag): Remove additional debug prints
2024-10-02 feat(short): Short circuit detection working well
    [main.cpp, tmc_control.cpp, tmc_control.hpp]
2024-10-02 feat(open): Open circuit first pass - working well
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2024-10-08 feat(buzzer): Pass TMC error state to buzzer
    [buzzer_control.cpp, main.cpp]
2024-10-08 fix(algo): Algo should only run when driver enable
    [buzzer_control.cpp, main.cpp, tmc_control.cpp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]
2024-10-08 fix(buzzer): Issue with double button press reqd
    [buzzer_control.cpp, main.cpp]
2024-10-08 feat(adc): VBat monitoring in place
2024-10-12 feat(algo): Low RPM case buffered out
2024-10-12 chore(tmc): Revert IRUN to 20 (was 31 = MAX)
    [tmc_control.hpp]
2024-10-12 docs(tmc): Peak current is 1.2Arms (not 1.4)
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2024-10-13 Revert "feat(usb): Detect USB voltage"
    This reverts commit 041d8bf6bf246d9a09a0e91fc6fe5f10c88520a7.
    [main.cpp]
2024-10-13 Revert "feat(usb): Detect USB voltage"
    This reverts commit 7223d5a14620702d62230eb0071ccfcc04d671a4.
    [main.cpp]
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2025-01-11 feat(vusb): Vusb monitoring
    NOTE: Requires NO PULL to correctly read voltage on input pin. Also
    applying this to button read pin.
    [main.cpp]
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2025-01-22 feat(tmc): Irun to Amps helper method
    Also, renamed pins_definitions.h to board_definitions.h as this contains
    more than just pinout information
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2025-03-06 feat(usb): Detect logic working well
    Interrupt used to detect USB pin & static volatile bool used to hold usb
    state
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2025-03-23 migrate(sdk): Up-rev to v2.1.1
    Using new Pico VS Code plugin, works well!
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2025-03-23 fix(irq): Fix vusb double interrupt
    [joystick_control.cpp, main.cpp]
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2025-04-14 feat(build): Smart build # increment
    Uses GIT_HASH:BUILD_NUMBER format for each firmware build. Added rev3 of
    PCB.
2025-04-14 feat(pin): Event mgr passes pin context to alarm
    This is a neater approach, the interrupt passes object instance context
    to the downstream debounce alarm to allow it to immediately target the
    correct pin object vs re-iterating over a for loop - noice
    [buzzer_control.cpp, buzzer_control.hpp, main.cpp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]
2025-04-14 feat(buzz): Fixed buzzer freq implementation
    [buzzer_control.cpp, buzzer_control.hpp, led_control.cpp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]
2025-04-15 feat(on): LED & Buzzer start after power ON
    [main.cpp]
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2025-04-15 feat(pwr): Vmot threshold wider range + fixes
    [board_definitions.h, main.cpp, pin_event_manager.hpp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]
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2025-04-17 fix(typo): Remove test code
    [led_control.cpp]
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2025-04-29 fix(buzzer): Re-instate buzzer pin
    [board_definitions.h]
2025-05-01 fix(motor): Joystick press now reset movement
    [main.cpp, tmc_control.cpp, tmc_control.hpp]
2025-05-01 feat(stall): Motor stall detect & velocity control
    [main.cpp, tmc_control.cpp, tmc_control.hpp]
2025-05-02 feat(speed): Max speed capping for large motors
    Includes quieter notification for stall event and quicker resolutions
    for detected stalls by increasing tcoolthrs value from 70 -> 150.
    [main.cpp, tmc_control.cpp, tmc_control.hpp]
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2025-07-20 test(bzl): Update testing framework to bzlmod
    Remove WORKSPACE file (now outdated) in favor of bzlmod usage.
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2025-07-22 wip(sdk): Cut back to a fixed version of the SDK
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2025-07-23 feat(volt): Space out ADC reads on first pass
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2026-03-17 wip(buzz): CMake ifdef for buzzer control
    [buzzer_control.cpp]
2026-03-17 feat(buzzer): CMake flag sets buzzer function
    [buzzer_control.cpp]
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2026-03-18 chore(obj): Move PowerControl from dyn to static
    Remove use of "new" keyword and create static references of PowerControl
    class for memory safety. Also, remove use of USB pin interrupt.
2026-03-20 feat(debug): Working again!!!
    launch.json is a bit messy with absolute paths but hopefully can resolve
    with a bit more trial+error.
    [main.cpp]
2026-03-20 feat(debug): launch.json template and README edit
    Best approach (so far) for enabling debugging and handling absolute path
    references from current code repo to what CMake build output symbol
    paths are looking for!
2026-03-22 feat(hook): Overflow and Mallow fail hooks impl
    [main.cpp]
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2026-03-24 feat(speed): Remove auto speed reduction mid stall
    Also reduced velocity step increment size and max motor speed.
    [main.cpp, tmc_control.cpp, tmc_control.hpp]
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2026-03-25 Revert "chore(pwm): Reinstate pwm_enable for LED to work"
    This reverts commit 7669f88be56d7a740e4529f2ccb09a9d0be65d12.
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2026-03-26 docs(update): Large overhaul of all docs + images
    Added Hardware folder for 3D print files and PCBA files alongside
    respective README's and annotated files - still WIP.
    [Bambu Labs Project - Enclosure.3mf, Bambu Labs Project - LED Box.3mf, Bottom.stl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]
2026-03-26 feat(error): Weak error handling function in main
    [joystick_control.cpp, led_control.cpp, main.cpp]
2026-03-26 feat(error): Handler functionality working well
    Increased Watchdog timeout to 6 seconds to accommodate 5 second blink
    and buzzer sequence in event of error handler. Also, added _breakpoint()
    in handler for debugger to catch.
    [main.cpp]
2026-03-26 feat(error): Avoid bootlooping with WDog disable
    [main.cpp]
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2026-03-27 chore(buzz): Fixed issue with CMake buzz disable
    [board_definitions.h, buzzer_control.cpp, led_control.cpp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]
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2026-03-27 feat(tmc): Fix no velocity change when stall occurs
    [board_definitions.h, main.cpp, tmc_control.cpp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]
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2026-03-27 feat(pcba): Added PCBA files for v0.4 of PCB
    [StepUp-B_Courtyard.gbr, StepUp-BottomLayer_Mask_Mask.gbs, StepUp-BottomLayer_Paste_Paste.gbp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]
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2026-03-31 docs(v1.0): Manufacturing file updates + README
    [BoM - Hand Assembly components.csv, PCBA.csv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]
2026-03-31 Update README with detailed programming and control steps
    Clarified instructions for programming and motor control.
2026-03-31 Revise StepUp! assembly guide
    Updated the StepUp! assembly guide with detailed instructions and images for assembly processes.
2026-04-21 fix(led): Activity updates now handled correctly
    [led_control.cpp]
2026-05-02 Revise motor control requirements in README
    Updated the explanation of the requirements for controlling motors, emphasizing the need for a simpler, intuitive approach.
